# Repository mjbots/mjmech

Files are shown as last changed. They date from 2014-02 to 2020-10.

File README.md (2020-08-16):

mjmech
======

Source and design files for various walking robots, their controlling
interfaces, and utilities for developing and operating them.

* GitHub https://github.com/mjbots/mjmech
* Most files are free hardware and software: Apache 2.0 License
* buildkite 

Directory structure
-------------------

* **base/** - C++ source files common to many applications.
* **ffmpeg/** - C++ ffmpeg wrappers.
* **gl/** - C++ GL wrappers.
* **mech/** - C++ source files specific to walking robots.
* **simulator/** - C++ source files for a quadruped simulator.
* **utils/** - Utilities for development and data analysis.
* **video-ui/** - Client application for FPV and real-time control.
* **configs/** - Configuration files for different robots and applications.
* **hw/** - Hardware design files along with firmware.
* **docs/** - Documentation.

First Time Setup
----------------

The following should work on Ubuntu 18.04

```
./install-packages
```

Building for host
-----------------

```
tools/bazel test //...
```

Running simulation
------------------

```
./bazel-bin/simulator/simulator -c configs/quadruped.ini
```

Then point your web browser to `http://localhost:4778`

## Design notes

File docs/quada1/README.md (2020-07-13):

# Getting started with the quad A1 #

## Safety ##

The mjbots quad A1 is a high performance robot capable of very fast
and powerful motions.  It is not recommended for use in the vicinity
of untrained personnel and especially not children or others who do
not appreciate what it is capable of.

Minimize physical handling of the robot while the power switch is on,
as malfunctions may cause legs to to move rapidly, creating pinch
hazards.

## Turn on ##

1. Ensure the switch is in the "off" position.  When off, the LED side of the switch is *not* depressed.

2. Insert a 4Ah ONE+ battery.  It may be necessary to apply a moderate tap with your fist in order to get both retaining clips to latch.

3. Flip the quad A1 over to be right side up and extend legs to be maximally stretched out, flat against the ground.  This is the "turn-on" position.
  * NOTE: The software is able to detect *some but not all* invalid
    turn-on positions.

4. Activate the power switch.  This means pressing the side with the LED down.

5. After ~30s, the robot's wifi access point will become available.  Connect to it.

6. Point your web browser to http://192.168.16.47:4778

## Joystick ##

The web control application supports a connected gamepad, which is the
simplest means of controlling the robot.  The "Y/4" button on the
gamepad enables mode select, while the d-pad up and down allow you to
cycle between modes.  Once you pick a mode that is not "Stop", the
quad A1 will stand up.

While moving, the left analog stick controls translation, while the
left and right motion of the right analog stick controls yaw.

When stopped, the left trigger can be pulled to enable "emote mode".
In that mode, the analog sticks control the attitude of the body.

## Keyboard ##

It is also possible to operate the robot with a mouse and keyboard.
The mouse can be used to click and select a mode.  WASDQE keys can be
used to pilot the quad A1 as per the on-screen display.

# Maintenance #

## Belt tension ##

The leg belts need to be kept appropriately tensioned to minimize the
possibility of belt skipping, while not overly stressing the 3d
printed upper leg structure.  The M3 adjustment bolt in each leg can
be used to adjust that tension.  As the belts stretch with age, it
will likely be necessary to use a longer bolt than the M3x12 initially
installed.  M3x14 is the longest suitable bolt.

When tensioned properly,

## Rezeroing leg ##

If the leg is disassembled or re-assembled, or the belt skips, then that leg will need to be re-zeroed.  This can be accomplished as follows:

1. Lay the quad A1 upside down on a flat surface.
2. Install the leg zeroing fixtures on the leg in question.  The lower
   leg qdd100 rests on the curved part of the large fixture, and the
   upper part restrains the upper leg.
3. The smaller fixture registers the upper and lower leg together.
   Slide it down as far as possible, then attempt to get the lower leg
   as centered as possible in any remaining play.
4. Connect to the robot and stop the existing software:

```
ssh -i mjmech/utils/ssh/mjbots.ssh pi@192.168.16.47
sudo screen -r
<CTRL-c>
```

5. Determine the leg number of the leg to be rezeroed.  When looking
   from the top, the legs are numbered as follows (note the robot is
   upside down now, so this will be mirrored):

```
   1      2

     FRONT

     BACK

   3      4
```

6. Determine which servos are associated with that leg:

```
Leg 1: 1-3
Leg 2: 4-6
Leg 3: 7-9
Leg 4: 10-12
```

7. Rezero the leg, using the servo numbers from above.

```
./moteus_tool -t1-3 --zero-offset
```

8. If more legs need to be rezeroed, the fixture can be moved between
   legs and the step 7 command run more as necessary.

9. Shutdown the computer, wait 15s, then turn off the power switch.

```
shutdown -h now
```

10. At this point the quad A1 can be set in the "turn-on" position and
    started up as normal.

## Change ssh key ##

The quad A1 is initially provisioned with an ssh key that is common to
all machines.  This is not normally a problem, as the SSID is unique
and the password is secret.  If you wish to expose the quad A1 to a
wider network, first contact info@mjbots.com to discuss your risk
profile.  Second, you may wish to change the default ssh access key.

First, use `ssh-copy-id` to install a new key on the quad A1:

```
ssh-copy-id -o "-i utils/ssh/default.ssh" pi@192.168.16.47
```

Then, ssh in, and remove the old key.

```
ssh pi@192.168.16.47
vi .ssh/authorized_keys  # remove the info@mjbots.com line
```

## Upgrading software ##

1. Compile:

```
tools/bazel build --config pi -c opt //mech:quad_deploy.tar
```

2. Copy it to the robot:

```
rsync -Pv -e "ssh -i utils/ssh/default.ssh"  \
  bazel-out/armeabihf-opt/bin/mech/quad_deploy.tar pi@192.168.16.47:
```

3. Perform the upgrade and restart the software.

NOTE: If any configurations have been modified, you will want to
manually capture those now, as this process will reset all
configuration to factory default.

```
ssh -i utils/ssh/default.ssh pi@192.168.16.47
sudo screen -r
<CTRL-c>
cd /home/pi
sudo -u pi tar xvf quad_deploy.tar
sync
cd mech
./start-robot.sh
<CTRL-a d>
```

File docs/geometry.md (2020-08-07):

# mjmech geometry #

## Unit naming conventions ##

Quantities expressed in a certain unit should have that unit included
as a suffix that variable name.

## Frame naming conventions ##

Quantities which are expressed relative to some frame or frames have those frames suffixed on the variable name using the simbody conventions :https://simtk.org/docman/view.php/47/231/SimbodyTheoryManual.pdf

As there, common frames may be abbreviated with a single uppercase
letter.

## Frame conventions ##

Coordinate systems are right handed, if there is a human associated
direction, they should be interpreted as:

* x is positive forward
* y is positive right
* z is positive down

## Common frames ##

Joint Frame (J): Each joint has a frame located at the center of
rotation of the shoulder, with +x facing outward, +y facing right, +z
facing down.

Leg Frame (G): The leg frame is located at the center of the shoulder
joint, with +x facing forward, +y facing right, and +z facing down.

Body Frame (B): This frame is oriented at the center of the quadruped
body and fixed to the chassis.

CoM Frame (M): This frame is fixed to the chassis at the center of
mass as measured with the legs in idle position.  It is oriented to be
level with the ground, so +Z is always down w.r.t. gravity.  The frame
has a yaw such that +X is pointed to same heading as Body +X.

Attitude Frame (A): This frame is fixed to the chassis center of mass.
+Z is down w.r.t. gravity.  The rotation of +X/+Y is arbitrary at
power up, and follows the rotation of the B/L transform.

Robot Frame (R): This frame is offset from the Body Frame (B) and
referenced in the same manner, but may be offset or rotated to apply
cosmetic kinematic changes.

Terrain Frame (T): This frame is located at the center of mass,
projected along the body Z direction at the ground location.  It is
oriented parallel to the local ground terrain and rotated to be
consistent with the M frame.

Local Frame (L): This frame is oriented such that down is parallel to
gravity.  Other degrees of freedom are initialized with the quadrupeds
body center at turn on, and have no absolute correlation with the
outside world.

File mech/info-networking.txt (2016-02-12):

Networking setup for mjmech

================
High level goals
================

 (1) A reliable video and control channel which works even when 2.4GHz band is
     very busy.

 (2) A way to upload/debug new code. Does not have to be as reliable.

===================
Implementable goals
===================

 - Use dual-band 802.11n cards. 'n' should give us stream diversity, while 5GHz
   band will be likely less congested.

 - Do not use WiFi association mechanisms, to make sure that short periods of
   total interference stay short.

 - Customize queue length and retransmission, to make sure that at least some
   video appears, and that the latency is not too high.

 - Be able to change the system properties reasonably fast (in under a
   minute, not during the match).

==============
Current Design
==============

We are using ad-hoc mode, but specifying all the parameters ourselves.
This should be enough to ensure that we can start communicating without having
to wait for other station, and that we will not re-negotiate mid links.

We are logging all the packets and measuring the latencies.

To set up, use the script 'setup_wifi_link.py'. All wifi details are there.

IP addressing:
 - Devices have IP in the 10.89.0.0/16 network
  - Well-known devices have short addresses:
     mjmech-odroid has 10.89.0.10
 - Multicast network is 239.89.108.0/24
   239.89.108.10:2720 is multicast announcements from odroid
   239.89.108.11:2721 is control commands

=================
Wifi card comments
=================

We want a wifi card that supports 5GHz and 802.11n, at least. These have
problems.

Driver: rt2800usb
~~~~~~~~~~~~~~~~~
uses in-tree driver.
works great, but only tested in adhoc mode.

Devices:
* AWUS052NH, "ID 148f:3572 Ralink Technology, Corp. RT3572 Wireless Adapter"
 - Large black/orange box with 2x external antennas, Mini USB B Female connector
 - Front: orange, blue LED, "ALPHA NETWORKS", curved vent slots
 - Back: black, slot for clip, "Model: AWUS052NH", S/N, MAC, etc..
 - Size: 84.8x62x2.53mm + 24x10x8mm USB cable + 2x R10x160 antennas

* DWA-160, "ID 2001:3c1a D-Link Corp. DWA-160 802.11abgn Xtreme N Dual Band Adapter(rev.B2) [Ralink RT5572]"
 - Large white dongle with black border, large strap attachment point on top
 - Front: "D-LINK", orange WPS button, orange LED
 - Back: "D-LINK DWA-160", "P/N CWA160CA.....B2 Model: DWA-160B2",
         "H/W Ver: B2", "F/W Ver: 2.40", S/N, MAC
 - Size: 68.4x28.2x12mm + 12x12x4.5mm USB A plug

Known problems:
* problems connecting to regular wifi (WPA2 client) -- link disappears
  in 10-60 seconds
 - suspect this is due to old kernel (3.8.13)
 - do not really care

Driver: rtl8812au
~~~~~~~~~~~~~~~~~
Out-of-tree driver from: https://github.com/gnab/rtl8812au.git

Devices:
* Edimax AC600, "ID 7392:a812 Edimax Technology Co., Ltd"
 - Black dongle with with strap attachment point on top
 - Front: "EDIMAX AC"
 - Back: "WPS" button, "EW-7811UTC", "FCC ID..", etc..
 - Metal part of USB connector: I/C, SN, MAC
 - Size: 25.6x15.6x7.5mm + 12.2x12x4.5mm USB A plug

Known problems:
* problems connecting to regular wifi (WPA2 client)
 - do not care
* does not use nl80211 ('iw' command)
 - script special-cases, uses iwconfig
* multicast does not work (no packets go out)
 - fixed by patching the source: set 'psta->state |= _FW_LINKED'
   in 'rtw_init_bcmc_stainfo'
* cannot specify multicast rate (always 6Mbit/sec)
 - no fix known
* cannot force ad-hoc connection -- no way to set bssid
 - no fix known

Driver: mt7610u
~~~~~~~~~~~~~~~
Out-of-tree driver from: https://github.com/coolshou/mt7610u

Also works for chipsets:
 RT2870 RT2770 RT307X RT2070
 RT357X RT3370
 RT8070 RT5X7X
 MT7610 MT7601 MT7612U

Devices:
* AC600 WiFi Dual Band USB Adapter UW-600M01 "ID 0e8d:7610 MediaTek Inc."
 - Black dongle with the small pinhole in the center of one side
 - Only words on device itself is "wifi AC"
 - Box says: STRONGR-R AC600 / UW-600M01
 - Size: 15.1x14.9x8.1mm + 11.7x12x4.6mm USB plug

Potential other devices
~~~~~~~~~~~~~~~~~~~~~~~
This list is to filter out the devices which are not interesting for some reason
Hist: amazon search for "dual band wifi usb"

- Satechi Wireless Mini Dual Band Wi-Fi USB Mini Adapter ST-UMWAC
  rtl8812au according to amazon comments

- BlueFire Mini 150M USB WiFi Adapter B012G7H1YC
  not actually dual-band (2.4GHZ only)

- Glam Hobby 600Mbps AC600 Dual Band USB WiFi Dongle B011T5IF06
  driver link points to rtl8811au

- TRENDnet TEW-804UB Dual Band USB WiFi
  driver mentions RTL8811au, USB 20f4:804b

- Linksys Wireless Mini USB Adapter AC 580 Dual Band (AE6000)
  driver contains "RT2870" strings
  actual device is 13b1:003e, which seems to require mt7610u

- Sabrent AC600 Dual Band Wi-Fi USB Mini Adapter NT-WSAC
  driver file name is MT7601

- 'Intel Corporation Wireless 7260' (iwlwifi, integrated into thinkpad T430)
  does not support IBSS on 5GHZ band. Possible reason:
  "The firmware of (some?) Intel cards seems to prohibit the use of Band 2 in
  AP mode, and there is no workaround in driver or kernel code that I know
  of. "
  http://askubuntu.com/questions/457702/ubuntu-14-04-hostapd-802-11a-iwlwifi-no-ap

- "Motoraux 600Mbps Dual Band wireless" B0199FBBRM
 - driver unknown, TODO

- Woopower Wi-Fi Dual Band USB Adapter 5dBi Ext Antenna "AC600 MINI" B015SAFBRI
 - single external antenna
 - review has link to driver, which contains mt7610u code

- Bolse 300Mbps Wifi Wireless-N USB Micro Mini Adapter BO-N1557
 - has external antenna version (BO-N1559)
 - review says "Realtek RTL8192CU"

- Windrew 802.11AC 600mbps Dual Band 2.4G/5G UNT-W01
 - review says RT2870, other says to use driver for "EW-7711MAC"
 - this indicates mt7610u

- LB1 High Performance 600Mbps Dual Band USB UW-600M01-N0001
 - model number matches mt7610u part number

Testing wireless cards
~~~~~~~~~~~~~~~~~~~~~~
If you have a new wireless card, you can check it as following:

- Basic setup
(1) on main PC, set up wifi link and a monitor mode. run 'horst' on it.
 - In horst, enter 'ESSID' screen ('e' key), you should see the
   telemetry network.
 - bring wifi interface down on the main PC. the TSF value on horst will freeze.
 - bring wifi interface up on DUT.
 - Make sure TSF updates often and 'source' matches DUT's wireless MAC.
 - Make sure parameters (CH=channel, BSSID, BINT=beacon interval)
   match the configured ones.

(2) Start sending packets into 'empty space' (since PC has not joined yet)
 - In a new window:
tools/odroid/push-tree.sh odroid-mjmech \
  scons base/build-armv7l/udp_manual_test '&&' \
   base/build-armv7l/udp_manual_test -v \
      --link1.send_interval_s 0.005 --link1.source 239.89.108.11

 - The windows will print statistics every 10 seconds. Make sure packets are
   being sent. We do not expect to recevie anything at this time. Make sure it
   can maintain the send rate (there will be warnings if it cannot)
  INFO[link1]: stats: tx_count=2000 tx_size=2000000

 - In horst, switch to 'Stats' ('a' key)
  - You may want to 'R'eset the stats
  - Make sure prevalent rate is as configured in python (24M)
  - Make sure 'Retries' is very low and not growing.
  - Make sure 'Total bits/sec' is correct: 1.5M = 1000 bytes * 200 Hz
  - Make sure 'Total usage' is reasonable (for configuration descirbed above,
    it is 9-10%)

(3) on main PC, bring the wireless interface back up.
 - Make sure you can ping 10.89.0.10
 - On horst ESSID screen, make sure channel/BSSID did not change.

(4) Start sending
 - Window 1:
scons -j4 base/build-x86_64/udp_manual_test && \
   base/build-x86_64/udp_manual_test -v \
       --link1.send_interval_s 0.005 --link1.dest 239.89.108.11

 - Both windows will print statistics every 10 seconds. Make sure the packet
   loss is not excessively high:
  INFO[link1]: stats: rx[1]=1980 rx_count=1980 rx_size=1980000 tx_count=2000 tx_size=2000000

 - In horst, switch to 'Stats'.
  - Make sure rate and retries are still correct.
  - The 'Total bit/sec' will double.
  - The 'Total usage' willb bigger -- for configuration descirbed above, it is 24-25%

(5) Bring down the wireless interface on the main PC again.
 - Make sure the packets are still being sent as in item (2)

==============
Other options:
==============

Security
~~~~~~~~

We have to think about security -- in the large event, there may be all sorts
of people.

For reliability, we cannot use stateful security like WPA/WPA2. We may use WEP
eventually, but it will be disabled initially to simplify troubleshooting.

Attack: taking over robot
Status: not relevant -- we already use SSH to upload; assuming that our
application is not stupidly insecure, it will not provide any access to the
robot' OS.

Attack: taking over controlling laptop
Status: uses either our app or existing servers; our app should be fine, as long
at it is not stupidly unsecure; as for other apps, it is not worse than using
laptop in the coffee shop.

Attack: Denial of service.
Status: very likely possible, esp. if we crash on invalid packets. But wifi is
easily jammable anyway anyway. TODO theamk finish

Attack: information disclosure
Status: whatever. We have no confidential info over the channel (unless a
competitor incorporates it in their UI :) )

Robot link setup
~~~~~~~~~~~~~~~~

Our only option is usb<->wifi cards -- the robot has no other fast exposed
buses, and integrated wifi is not present / not dual-band.

Base station setup
~~~~~~~~~~~~~~~~~~

We need to be able to fully control base stations (obviously venue's AP will
not work, or may not be present at all). The options are:

- Dedicate a router for base station, hook it to laptop via ethernet.
 - PRO: may have very little latency if we write on-router daemon and card is
        connected via PCI.
 - PRO: nothing interferes with wifi setup
 - PRO: may be placed very close to the stage
 - CON: need to setup packet forwarding or write on-router daemon
 - CON: the dual-band N models may be large, require external power

- Use external USB card
 - PRO: small size, no external power supply needed.
 - PRO: May use the same type of the card the mech uses.
 - CON: USB adds some latency.
 - CON: NetworkManager will interfere.
  - Disable it completely (annoying as built-in wifi may be used during
    development / debugging).
  - May use network namespaces
   - This requires that anything that wants to talk to it has a root access.
   - Or we need to setup a 'virtual router' that needs the same
     packet-forwaring setup or router daemon that physical router requires.
  - May just add card's MAC to networkmanager ignore file
   - This is tricky to get right. Should probably script this.

- Use laptop's integrated network card
 - PRO: lower latency than USB-based cards
 - CON: intervet will not work if integrated card was used for it.
 - PRO: can just disable networkmanager's wifi entirely.
 - CON: not sure how good integrated antenna is.
 - CON: laptop's card may not be good enough, and we won't be able to use it.

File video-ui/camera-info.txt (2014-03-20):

Driver Info (not using libv4l2):
	Driver name   : uvcvideo
	Card type     : HD Pro Webcam C920
	Bus info      : usb-s5p-ehci-3.2
	Driver version: 3.8.13
	Capabilities  : 0x84000001
		Video Capture
		Streaming
		Device Capabilities
	Device Caps   : 0x04000001
		Video Capture
		Streaming
Priority: 2
Video input : 0 (Camera 1: ok)
Format Video Capture:
	Width/Height  : 1920/1080
	Pixel Format  : 'H264'
	Field         : None
	Bytes per Line: 3840
	Size Image    : 4147200
	Colorspace    : SRGB
Crop Capability Video Capture:
	Bounds      : Left 0, Top 0, Width 1920, Height 1080
	Default     : Left 0, Top 0, Width 1920, Height 1080
	Pixel Aspect: 1/1
Streaming Parameters Video Capture:
	Capabilities     : timeperframe
	Frames per second: 30.000 (30/1)
	Read buffers     : 0
                     brightness (int)    : min=0 max=255 step=1 default=128 value=128
                       contrast (int)    : min=0 max=255 step=1 default=128 value=128
                     saturation (int)    : min=0 max=255 step=1 default=128 value=128
 white_balance_temperature_auto (bool)   : default=1 value=1
                           gain (int)    : min=0 max=255 step=1 default=0 value=201
           power_line_frequency (menu)   : min=0 max=2 default=2 value=2
      white_balance_temperature (int)    : min=2000 max=6500 step=1 default=4000 value=2354 flags=inactive
                      sharpness (int)    : min=0 max=255 step=1 default=128 value=128
         backlight_compensation (int)    : min=0 max=1 step=1 default=0 value=0
                  exposure_auto (menu)   : min=0 max=3 default=3 value=3
              exposure_absolute (int)    : min=3 max=2047 step=1 default=250 value=416 flags=inactive
         exposure_auto_priority (bool)   : default=0 value=1
                   pan_absolute (int)    : min=-36000 max=36000 step=3600 default=0 value=0
                  tilt_absolute (int)    : min=-36000 max=36000 step=3600 default=0 value=0
                 focus_absolute (int)    : min=0 max=250 step=5 default=0 value=0 flags=inactive
                     focus_auto (bool)   : default=1 value=1
                  zoom_absolute (int)    : min=100 max=500 step=1 default=100 value=100

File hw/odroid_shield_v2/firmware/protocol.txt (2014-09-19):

The device shares the serial bus with herculex, so the protocol
is fulley herculex compatible.

AVR listens at 115200 (divisor 16 in high-speed mode, 2.1% error)

It does not handle broadcasts because this it too much pain.

The device sits on address 99, and supports the following commands:
  CMD_STAT
  CMD_REBOOT -- does not reboot, just clears outputs and error flags.
  CMD_RAMWRITE/CMD_RAMREAD -- limited addresses
    - read address and status

    - read/write LEDS (53):
      GREEN is green LED pin (nothing is there yet)
      RED   is laser output
      BLUE  is blue LED on the board
      unlike real servo, if no LED commands are given for few
      seconds, all LEDs are turned off

    - read/write FIRE TIME (80, reserved)
      This is 1-byte register which can be read and written.
      As long as it is non-zero:
       - FIRE PWM may be non-zero
       - Value decreases by 1 every 10 mS

    - read/write FIRE PWM (81, reserved)
      This is 1-byte register which sets PWM value for fire motor.
      (0 = off, 255 = continious high)
      It is continously forced to zero unless FIRE CONTROL is set.

    - read/write AGITATOR PWM (82, reserved)
      This is 1-byte register which sets PWM value for agitator motor.
      (0 = off, 255 = continious high)
      It is bound to LED activity -- if LEDs are not updated for a while,
      then this value is forced to zero. Thus, you will want to write
      to LED register at the same time as to this register.

    - LEDS alias: (83, reserved) -- exactly the same as 53
      allows one-command access to agitator pwm

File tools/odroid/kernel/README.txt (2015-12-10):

Compiling custom kernel

-----------------------------
Motivation:

The linux kernel in the odroid distribution we are using is based on 3.8.13.30
kernel modified by hardkernel. This has two problems:
(1) there is no 'build' directory, so it is impossible to build out-of-tree
drivers.
(2) some wireless drivers are too old (such as rt2800usb)

There are some instructions on how to partially rebuild a kernel to fix (1),
but if we are going to make our own kernel, we migh t as well go to mainline.

Stock kernel info:
uname: 3.8.13.30 #1 SMP PREEMPT Fri Sep 4 23:45:57 BRT 2015 armv7l armv7l armv7l GNU/Linux
vermagic (from modinfo): 3.8.13.30 SMP preempt mod_unload ARMv7 p2v8
ABI ('file' on module): 32-bit LSB relocatable, ARM, EABI5 version 1 (SYSV)
source: git clone https://github.com/hardkernel/linux.git -b odroid-3.8.y

Inspiration:
http://rglinuxtech.com/?p=1622 (and other posts on this blog)

Instructions:
https://mescanef.net/blog/2014/12/custom-kernel-compilation-for-odroid-u2-u3-on-host-running-fedora-linux/

-----------------------------
Preparation:
possibly "mainline kernels need an updated u-boot to successfully boot."
http://rtisat.blogspot.com/2015/04/a-little-progress.html

I updated the u-boot via odroid-utility.sh

luckily, initrd does not seem to contain any kernel modules.
check with:
dd bs=64 skip=1 if=/media/boot/uInitrd  | zcat | cpio --list | less

New kernel needs new u-boot, which can be updated per blog post above.
Run the following on the odroid:
    aptitiude install device-tree-compiler
    wget http://odroid.in/guides/ubuntu-lfs/boot.tar.gz
    tar xzf boot.tar.gz
    git clone https://github.com/tobiasjakobi/u-boot
    cd u-boot
    make odroid_config
    make
    cp u-boot-dtb.bin ../boot/u-boot.bin

    echo 0 | sudo tee /sys/block/mmcblk0boot0/force_ro
    sudo dd iflag=dsync oflag=dsync if=./u-boot-dtb.bin of=/dev/mmcblk0boot0 seek=62

    cd ../boot
    bash ./sd_fusing.sh /dev/mmcblk0

                        signed_bl1_position=0
                        bl2_position=30
                        uboot_position=62
                        tzsw_position=2110

(the old kernels still work after this procedure)
u-boot version after:
  Exynos4412 # version
  U-Boot 2010.12-svn (May 12 2014 - 15:05:46) for Exynox4412

uboot update: see /usr/local/bin/kernel_update.sh

-----------------------------
Process:
We do a cross-compile on a x86_64 machine.

(1) download the kernel, prepare the build dir
 sudo apt-get install gcc-4.7-arm-linux-gnueabi gcc-arm-linux-gnueabi
 # the kernels are extracted as root, and thus read-only. make the build dir.
 sudo install -d -o $UID /usr/src/kernel-odroid

(1a) get the stock kernel. note
 cd /tmp
 wget https://cdn.kernel.org/pub/linux/kernel/v4.x/linux-4.3.tar.xz
 sudo tar xJf linux-4.3.tar.xz -C /usr/src
  get the odroid kernel

(2) configure kernel:
note: always use 'kmake.sh' instead of make in kernel dir, or you many get
options related to x86 kernel. It also move .config file location inside
the tree, so 'git diff' becomes more helpful.

use previous configuration with new things set as modules:
 rm tools/odroid/kernel/config-linux-4.3
 KCONFIG_ALLCONFIG=$PWD/tools/odroid/kernel/config-hardkernel-3.8.13.30 tools/odroid/kernel/kmake.sh allmodconfig
OR use previous configuration with new things set as default:
 cp tools/odroid/kernel/config-hardkernel-3.8.13.30 tools/odroid/kernel/config-linux-4.3
 tools/odroid/kernel/kmake.sh olddefconfig

the enter/exit menunconfig to inspect it by hand and update the config:
 tools/odroid/kernel/kmake.sh menuconfig
 # pay attention to options with '(NEW)'
 # make sure to clear CONFIG_EXTRA_FIRMWARE if using mainline kernels
 # make sure to CONFIG_MODULE_COMPRESS is not set

(3) build and copy modules
 time tools/odroid/kernel/kmake.sh -j4 zImage modules
 tools/odroid/kernel/kmake.sh modules_install firmware_install zinstall

 # Check version
 tools/odroid/kernel/kmake.sh -s kernelrelease
 # optionally delete old modules
 rm /usr/src/kernel-odroid/linux-4.3-install/boot/*.old
 ssh odroid@odroid-mjmech rm -rf /lib/modules/4.3.0-mjmech1 /lib/firmware-linux-4.3
 # copy all files over (this will not activate them yet)
 rsync -av --rsync-path='sudo rsync' /usr/src/kernel-odroid/linux-4.3-install/ odroid@odroid-mjmech:/

 # copy to /boot partition
 odroid@odroid-mjmech# sudo cp /boot/exynos4412-odroidu3.dtb /media/boot/
 odroid@odroid-mjmech# sudo cp /boot/vmlinuz-4.3.0-mjmech1 /media/boot/zImage-4.3
 sudo mkimage -T script -d kernel-4.3.script kernel-4.3.scr

(4) activate the new kernel
 odroid@odroid-mjmech# sudo cp kernel-4.3.scr boot.scr
 odroid@odroid-mjmech# sudo reboot

--------
recovery procedure
- connect serial port, open at 115200
- press any key during countdown
- run the original boot script (old bootloader)
fatload mmc 0:1 40008000 boot-auto_edid.scr
run bootscript
# if the bootloader has been updated, the last step will fail; in this case, run:
bootz  0x40008000 0x42000000

- once booted, restore original script:
odroid@odroid-mjmech$ cd /media/boot
odroid@odroid-mjmech$ sudo cp boot-auto_edid.scr boot.scr
odroid@odroid-mjmech$ sudo /usr/local/bin/odroid-utility.sh
# select 'update bootloader'

- examine the current config (or just see the boot.scr file on original image)
Exynos4412 # printenv bootcmd
bootcmd=    cfgload; mmc rescan 0:1; mmc rescan 0:2;  if run loadbootscript_1;     then run bootscript;  else     if run loadbootscript_2;  |
Exynos4412 # cfgload
do_fat_cfgload : cmd = fatload mmc 0:1 0x41000000 boot.ini
reading boot.ini
** Unable to read file boot.ini **
Exynos4412 # printenv loadbootscript_1
loadbootscript_1=echo >>> Load Boot Script from mmc 0:1 <<<;fatload mmc 0:1 40008000 boot.scr
Exynos4412 # run loadbootscript_1
>>> Load Boot Script from mmc 0:1 <<<
reading boot.scr
Warning : Reads a file that is smaller than the cluster size.
380 bytes read in 34 ms (10.7 KiB/s)
Exynos4412 # printenv bootscript
bootscript=source 40008000
Exynos4412 # md 40008000 75
40008000: 56190527 379fda4f 3e2d7d52 3c010000    '..VO..7R}->...<
40008010: 00000000 00000000 39df7f05 00060205    ...........9....
40008020: 746f6f62 7263732e 726f6620 77205820    boot.scr for X w
40008030: 20687469 494d4448 74756120 72702d6f    ith HDMI auto-pr
40008040: 34010000 00000000 65746573 6920766e    ...4....setenv i
40008050: 7274696e 69685f64 22206867 66667830    nitrd_high "0xff

- run stored commands using different kernel name
setenv initrd_high "0xffffffff"
setenv fdt_high "0xffffffff"
setenv bootcmd "fatload mmc 0:1 0x40008000 zImage.0; fatload mmc 0:1 0x42000000 uInitrd; bootm 0x40008000 0x42000000"
setenv edid_load "drm_kms_helper.edid_firmware=edid/1024x768.bin"
setenv bootargs "console=tty1 console=ttySAC1,115200n8 ${edid_load} root=UUID=e139ce78-9841-40fe-8823-96a304a09859 rootwait ro  mem=2047M"
boot

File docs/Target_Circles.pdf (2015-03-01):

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

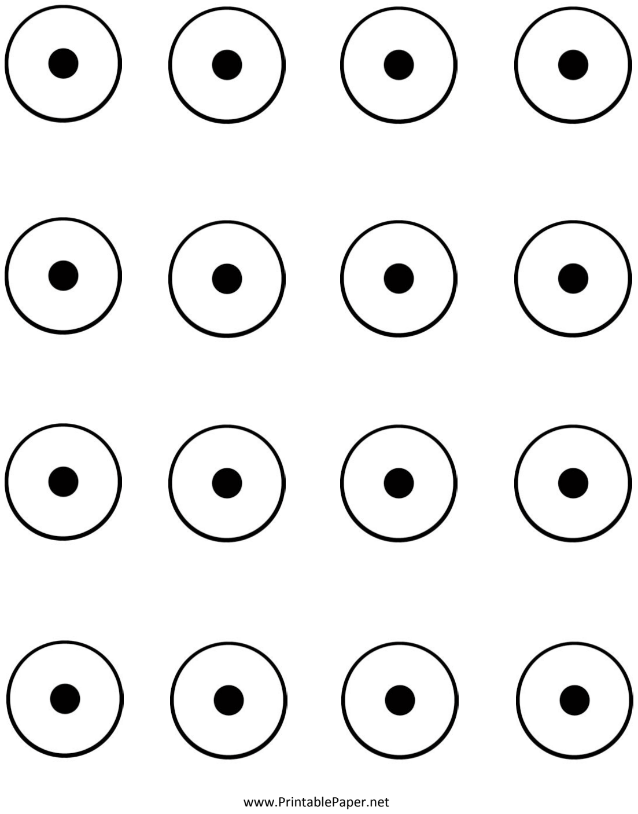
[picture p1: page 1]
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

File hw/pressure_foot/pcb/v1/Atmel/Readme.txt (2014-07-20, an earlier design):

						This CAD library is for CadSoft - EAGLE tool

How to import new library file (.lbr) into EAGLE:

1. Download and extract the file.
2. Copy the library file (.lbr) to EAGLE library folder; "C:\Program Files\EAGLE-X.XX.X\lbr" (X.XX.X is your EAGLE software version)
3. Start EAGLE software.
4. Under EAGLE Control Panel, go to the Library tree and browse for new copied library (.lbr) file.
5. Right click on the library and select "USE".
6. You have successfully imported new library and ready to use in your design.  

=============================================================================================================================================================

				For additional information, feedback and Technical support please contact reach from below:

Tech Support e-mail  ::	CAD_Tech@element14.com

----------------------------------------------------

Community website  

	http://www.element14.com/community/community/knode/cad_tools?view=overview

=============================================================================================================================================================

element14 Disclaimer :- 
 
This information has been provided to you free of charge for your use but remains the sole property of element14. While element14 has used reasonable efforts to ensure its accuracy, element14 does not guarantee that it is error-free, nor makes any warranty or guarantee as to the suitability of its schematics or footprints for any specific application. element14 reserves the right to make changes at any time without further notice. element14 expressly disclaims all implied warranties regarding this information, including but not limited to any implied warranties or merchantability or fitness for a particular purpose.
 
element14 will in no case be liable for your use, or the results of your use, of the CAD models or any accompanying written materials. It is your responsibility to verify the results of your use of this information in your own particular engineering and product environment and you assume the entire risk of doing so or failing to do so. 
 
Footprint designs were developed using standard layout guidelines for most common and practical applications. All schematic symbols, footprints and layer definitions should be validated by the customer’s own technical experts as application specific requirements may differ.

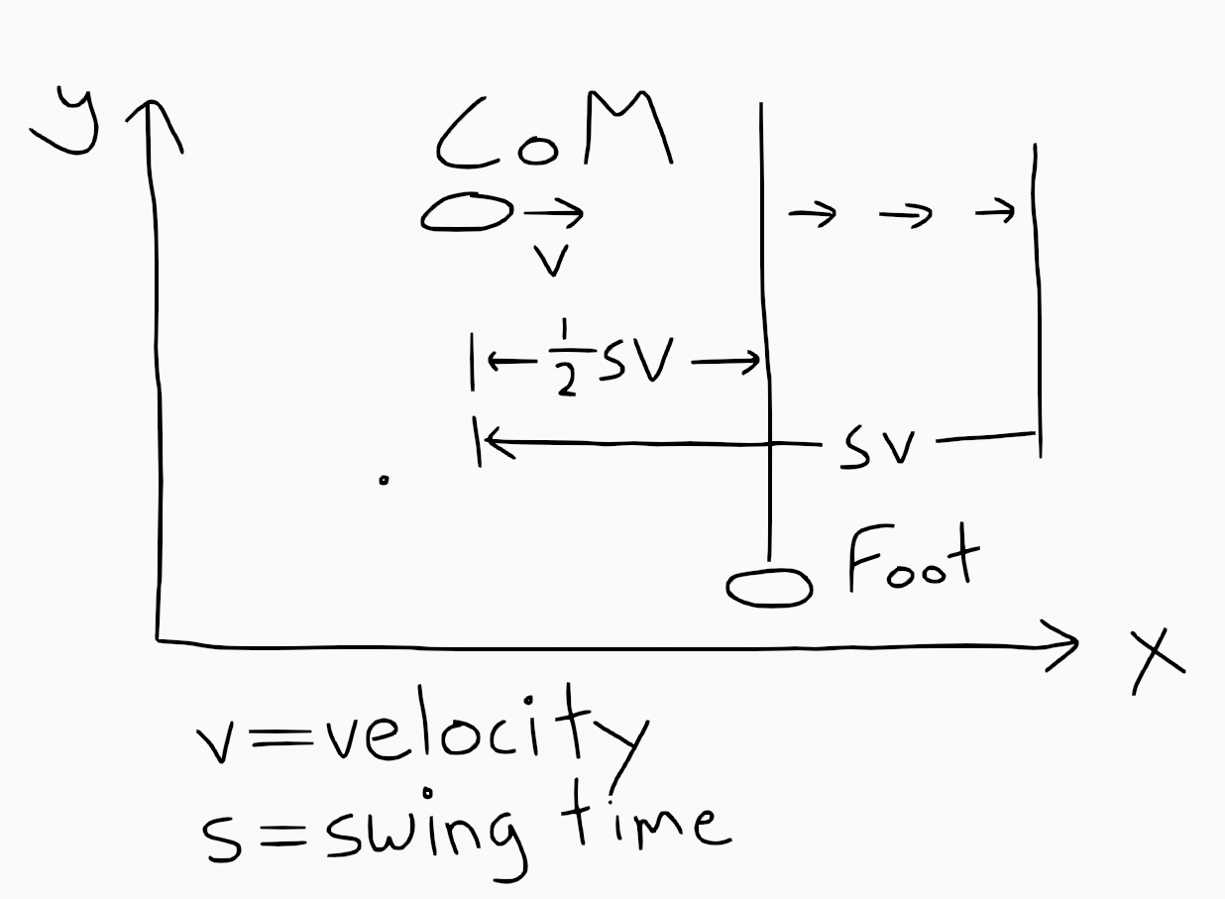
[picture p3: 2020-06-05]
docs/diagrams/1d_swing.png

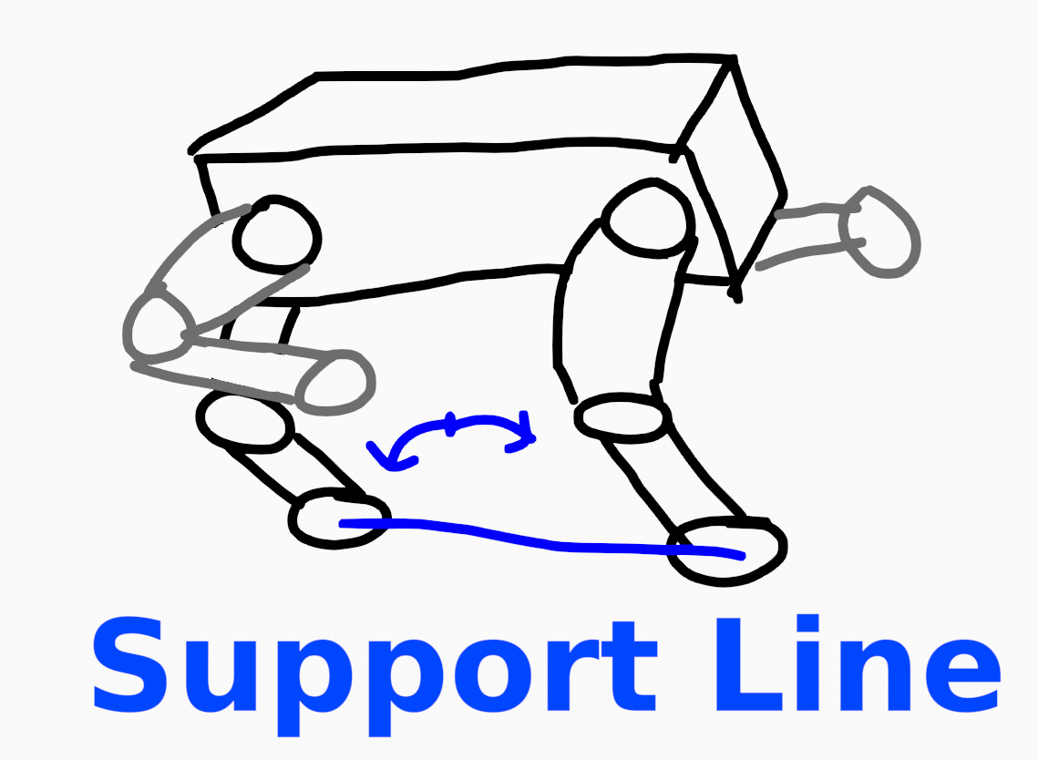
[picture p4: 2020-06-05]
docs/diagrams/support_line.png

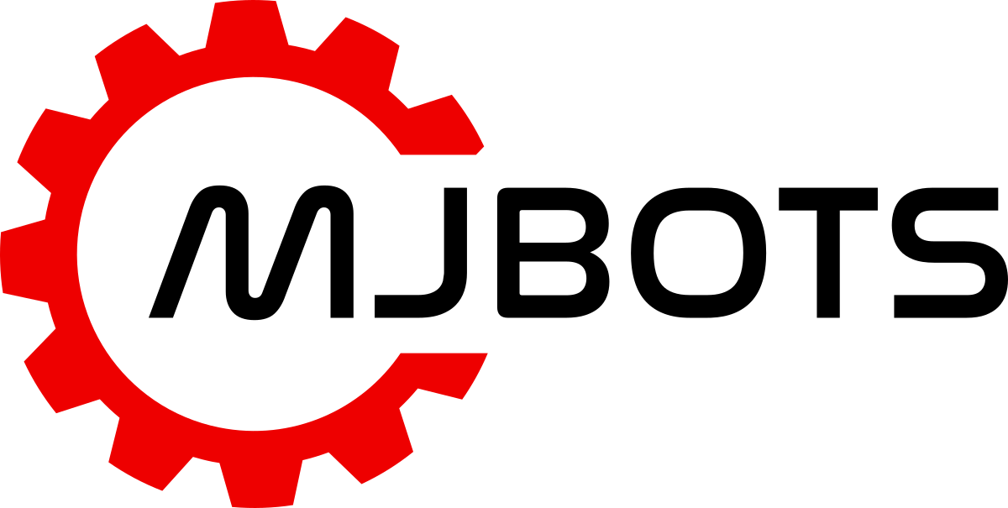
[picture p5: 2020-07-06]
mech/web_control_assets/mjbots.png

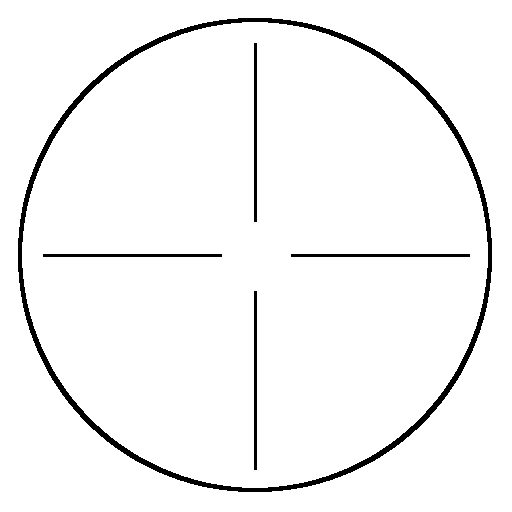
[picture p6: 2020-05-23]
mech/reticle.png

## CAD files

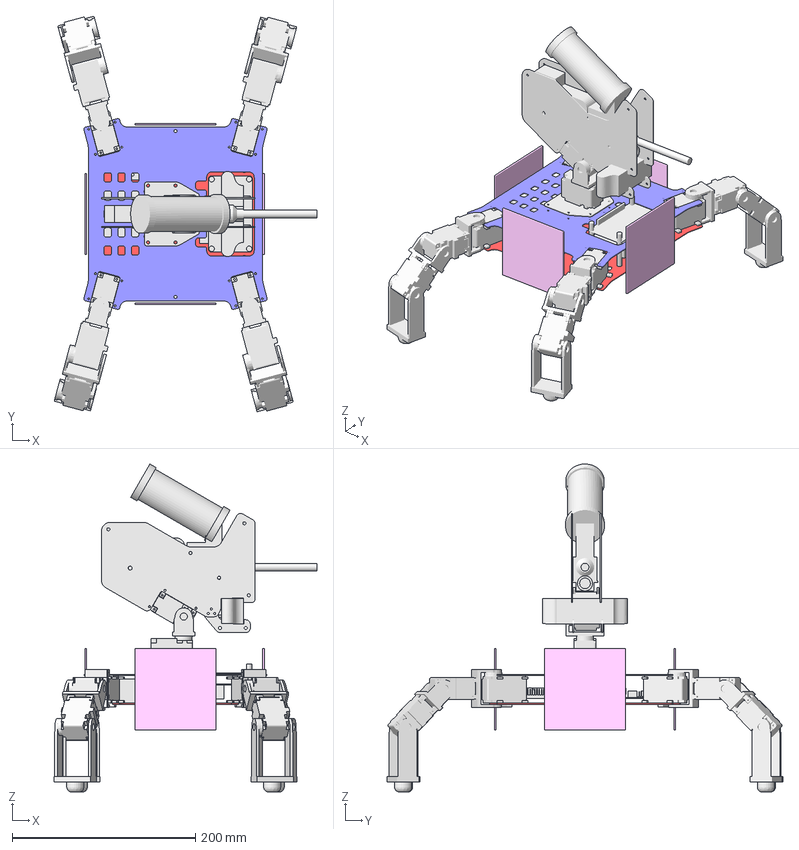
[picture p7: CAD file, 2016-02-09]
hw/chassis_lizard/freecad/chassis.fcstd
286.8 x 432.0 x 358.2 mm
pololu_driver
battery
power_dist
leg
scoring_transponder
leg2
leg3
leg4
sensor
sensor2
sensor3
sensor4
odroid
i_beam1
i_beam2
i_beam3
i_beam4
chassis_bottom_harness_holes
chassis_top_turret_holes
turret_plate_gimbal_holes
turret

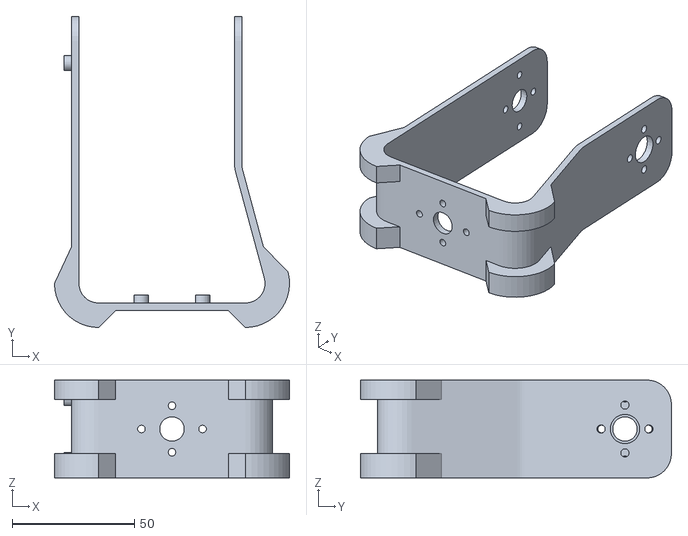
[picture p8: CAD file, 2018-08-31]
hw/chassis_mammal/freecad/gimbal_bracket.stl
96.0 x 127.0 x 40.0

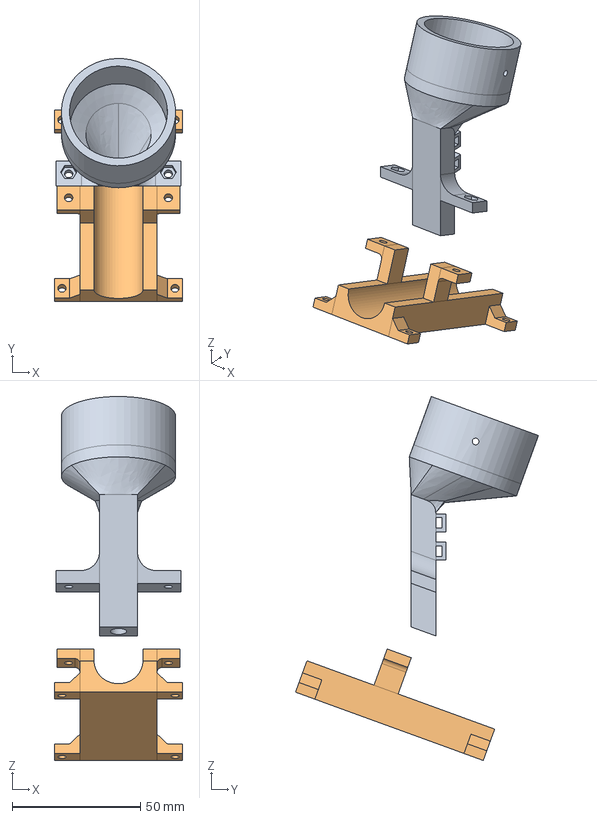
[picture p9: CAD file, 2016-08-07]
hw/panel_qual/freecad/gravity_feed.fcstd
50.0 x 94.6 x 141.7 mm

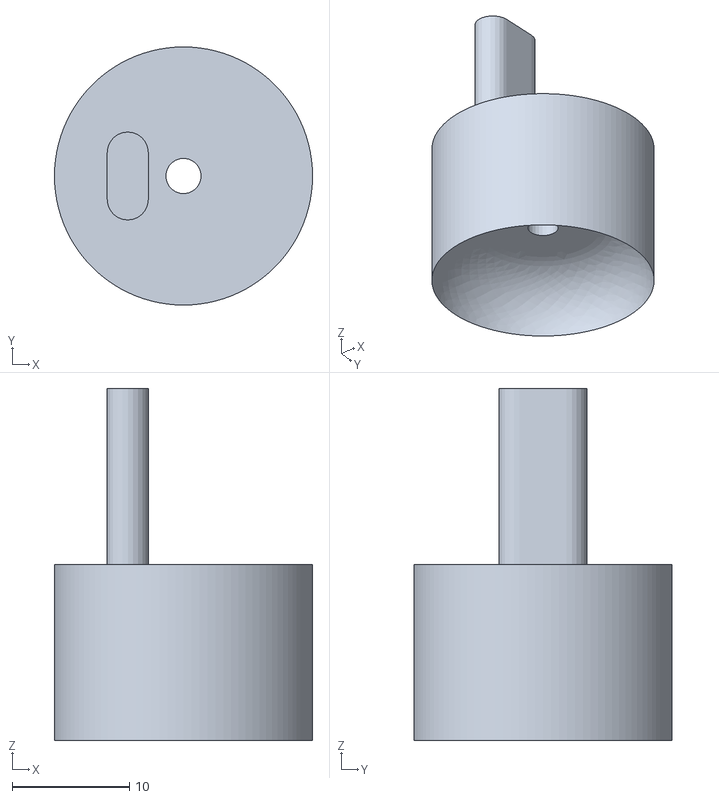
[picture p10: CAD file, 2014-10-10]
hw/pressure_foot/freecad/plunger.stl
22.0 x 22.0 x 30.0

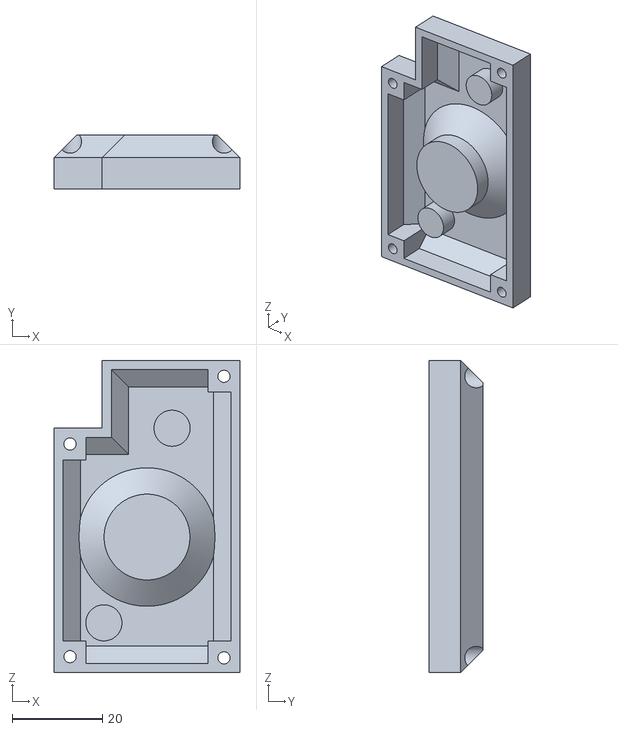
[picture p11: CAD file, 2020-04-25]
hw/turret/aeg_20200418/loader_cap.stl
41.1 x 12.0 x 69.1

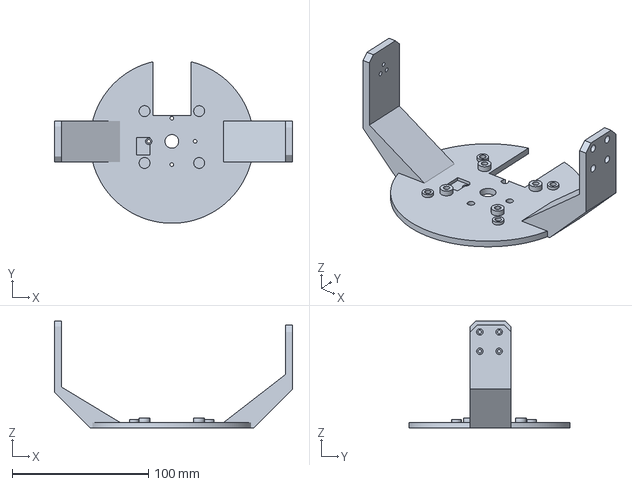
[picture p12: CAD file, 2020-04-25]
hw/turret/aeg_20200419/yaw_motor_plate.3mf
174.4 x 118.3 x 78.2 mm

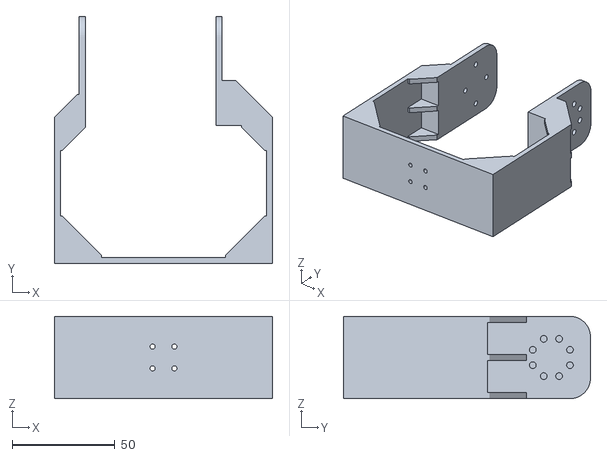
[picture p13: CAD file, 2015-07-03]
hw/turret/freecad/gimbal_bracket.stl
106.0 x 120.0 x 40.0

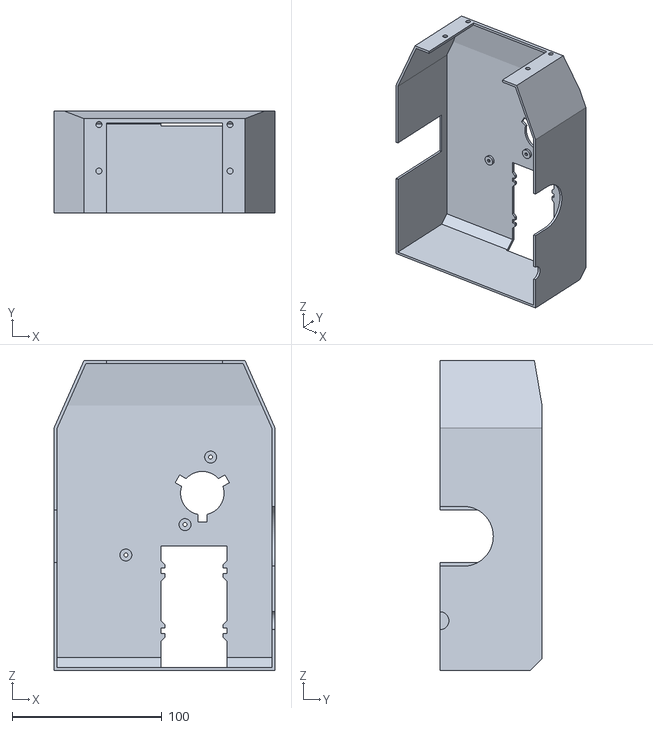
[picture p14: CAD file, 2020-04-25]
hw/turret/turret_20200420/shell_top.stl
147.6 x 68.2 x 207.1

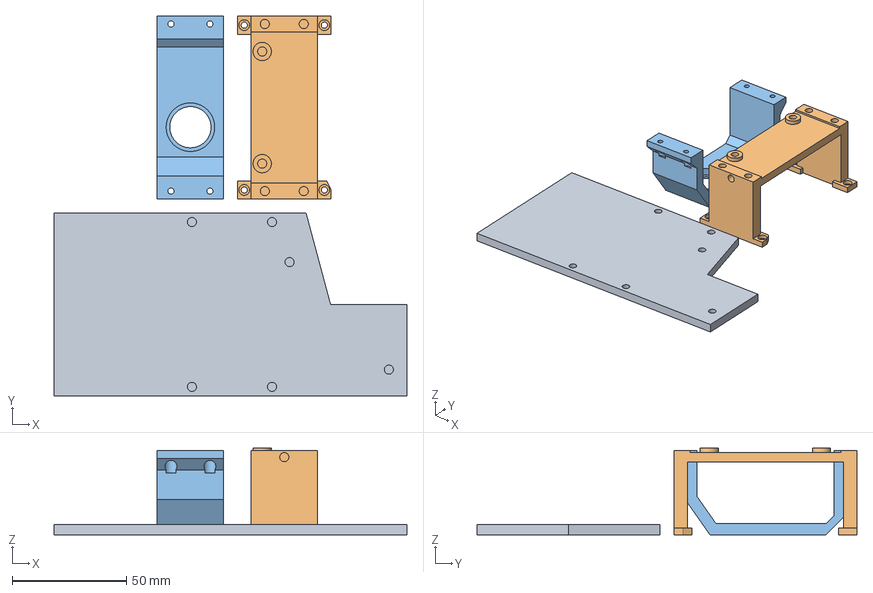
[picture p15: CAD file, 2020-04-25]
hw/turret/turret_20200421-2/mid_frame_right_frame_rpitch_plate.3mf
154.0 x 166.0 x 38.0 mm
mid_frame.stl
right_frame.stl
right_pitch_plate.stl

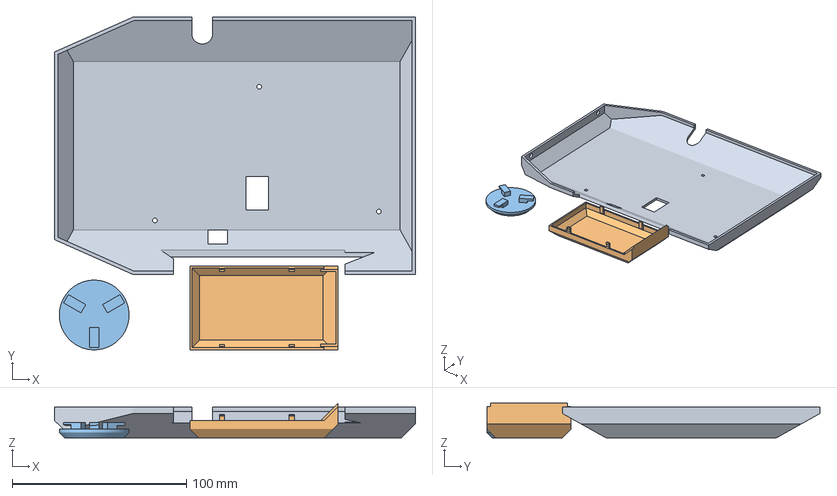
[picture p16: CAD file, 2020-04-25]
hw/turret/turret_20200421/shell_bottom_accessories.3mf
207.1 x 190.8 x 20.0 mm
shell_bottom.stl
shell_battery_cover.stl
shell_magazine_cover.stl

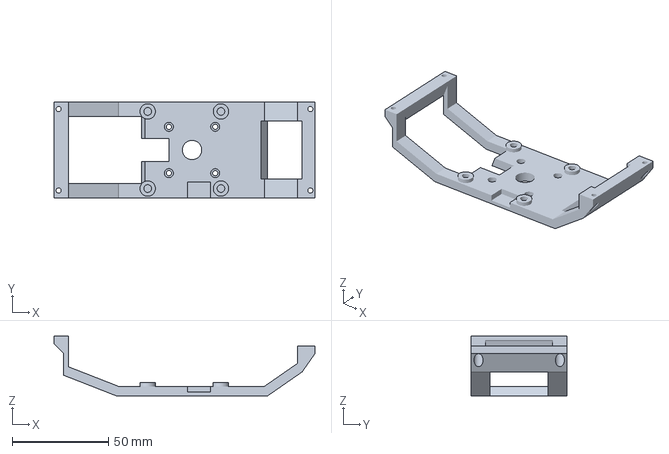
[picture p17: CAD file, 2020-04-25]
hw/turret/turret_20200422/pitch_motor_plate.3mf
135.5 x 50.0 x 31.1 mm

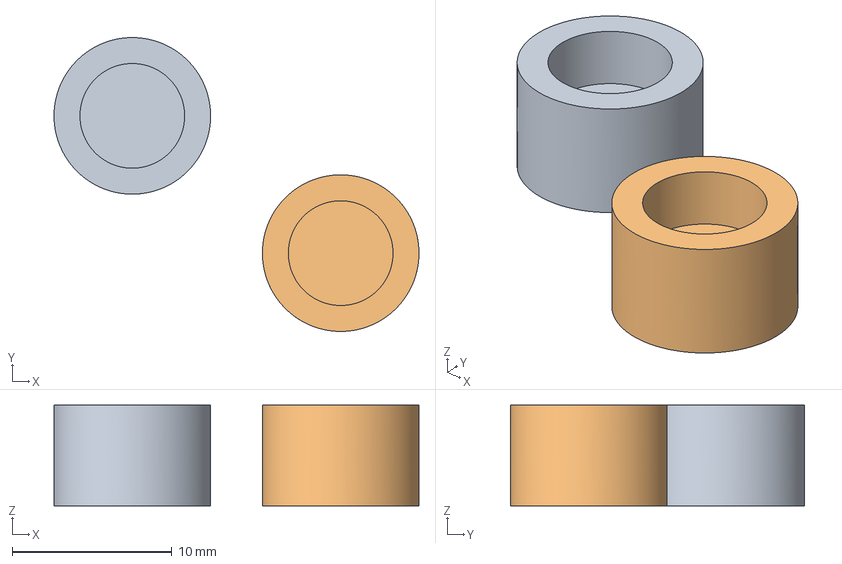
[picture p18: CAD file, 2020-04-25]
hw/turret/turret_20200423/magnet_holder.3mf
22.8 x 18.4 x 6.30 mm

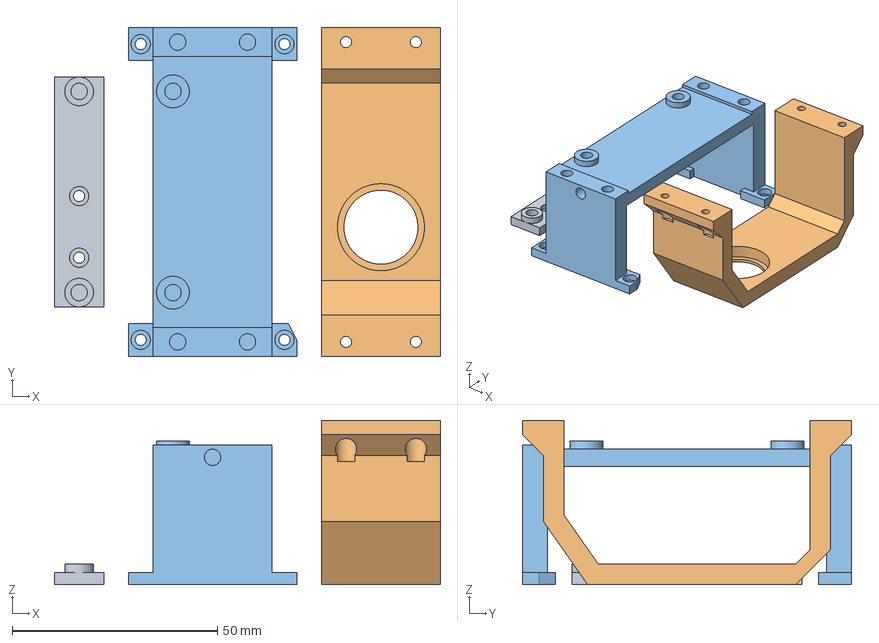
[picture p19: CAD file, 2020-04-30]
hw/turret/turret_20200430/right_brackets.3mf
94.0 x 80.0 x 40.0 mm
front_pi_bracket.stl
right_pitch_plate.stl
right_frame.stl

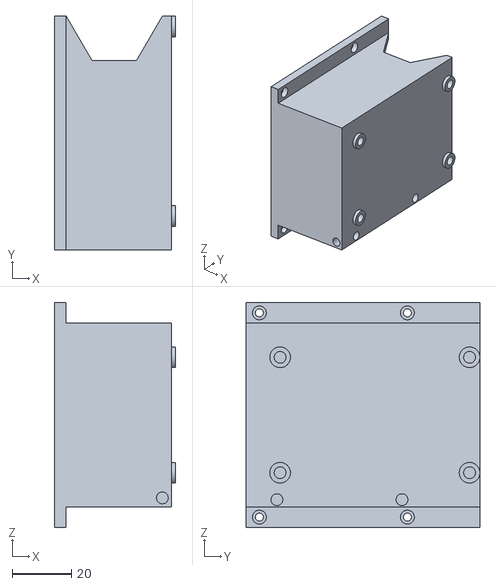
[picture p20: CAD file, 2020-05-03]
hw/turret/turret_20200501/battery_shelf.stl
41.0 x 79.0 x 76.0

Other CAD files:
hw/turret/turret_20200502/top.3mf
hw/turret/turret_20200516/battery_cover.3mf
hw/turret/turret_20200517/battery_cover_2.stl
hw/weapon/aeg_20200414-2/receiver.3mf
docs/diagrams/1d_swing.blend
docs/diagrams/support_line.blend
hw/chassis_lizard/freecad/battery.fcstd
hw/chassis_lizard/freecad/battery.step
hw/chassis_lizard/freecad/bracket_long_tip.blend
hw/chassis_lizard/freecad/bracket_long_tip.fcstd
hw/chassis_lizard/freecad/bracket_long_tip.iges
hw/chassis_lizard/freecad/bracket_short.fcstd
hw/chassis_lizard/freecad/bracket_short.iges
hw/chassis_lizard/freecad/bracket_short_0_join.fcstd
hw/chassis_lizard/freecad/bracket_short_0_join.iges
hw/chassis_lizard/freecad/bracket_short_90_join.fcstd
hw/chassis_lizard/freecad/bracket_short_90_join.iges
hw/chassis_lizard/freecad/bracket_u1.fcstd
hw/chassis_lizard/freecad/bracket_u1.iges
hw/chassis_lizard/freecad/bracket_u4.fcstd
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

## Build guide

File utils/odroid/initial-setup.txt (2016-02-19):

New Odroid setup procedure
Using Odroid U3+

(1) Start by plugging eMMC card into your computer. Get an small
"Ubuntu 14.04 Server" image from:
  http://forum.odroid.com/viewtopic.php?f=77&t=5123
  http://odroid.in/ubuntu_14.04lts/

mkdir -p /tmp/odroid-image && cd /tmp/odroid-image
wget http://odroid.in/ubuntu_14.04lts/ubuntu-14.04lts-server-odroid-u-20140604.img.xz
md5sum ubuntu-14.04lts-server-odroid-u-20140604.img.xz
# b7568e191eef679116e252ae5136ecee  ubuntu-14.04lts-server-odroid-u-20140604.img.x

  Then extract it to the eMMC card:
ls -l /dev/disk/by-path/*-usb-*:[0-9]
xzcat *lts-server*.xz | sudo dd bs=1M of=/dev/sdXX
# 3384803328 bytes (3.4 GB) copied, 268.485 s, 12.6 MB/s
sync

(2) Do the initial setup:
# Plug wired ethernet and power. Device should appear as 'odroid-server':
ssh -o UserKnownHostsFile=/dev/null -o StrictHostKeyChecking=no root@odroid-server
# password: odroid
odroid-utility.sh
# choose "4  Resize your root partition"
# choose "7  Change Hostname"
#  -> Examples below use "odroid-mjmech"
# choose "2  Update your Kernel/Firmware"
#  -> choose "1 Update Kernel"
#  -> choose "2 Install firmware files to /lib/firmware"
# exit all
useradd -Um odroid
chsh -s /bin/bash odroid
passwd odroid
visudo
# add the line:
  odroid  ALL=NOPASSWD: ALL
# logout, install ssh public key
ssh-copy-id -i ~/.ssh/id_dsa.pub odroid@odroid-mjmech
ssh odroid@odroid-mjmech sudo uptime

(3) Upload the code and configure the devices:
tools/odroid/push-tree.sh odroid-mjmech sudo tools/odroid/setup-system.sh
# if you this fails, ssh into device and run:
sudo apt-get update
sudo apt-get upgrade
sudo mjmech-clean/tools/odroid/setup-system.sh

(4) Setup wifi auth and reboot:
ssh odroid@odroid-mjmech -t sudo editor /etc/wpa_supplicant/wpa_supplicant.conf
ssh odroid@odroid-mjmech -t sudo reboot
# You may wish to unplug wired ethernet at this point.

(5) Do the initial build:
tools/odroid/push-tree.sh odroid-mjmech time scons
# real 41m45.404s / user 40m8.325s / sys 1m22.815s

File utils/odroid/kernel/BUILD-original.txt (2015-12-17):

Re-compiling original odroid kernel

STATUS: Successful -- system boots fine

-----------------------------
# Trying to follow instructions as close as possible:
#  https://mescanef.net/blog/2014/12/custom-kernel-compilation-for-odroid-u2-u3-on-host-running-fedora-linux/
# Differences:
#  (1) rpm ugliness since we are on deb system
#  (2) easier deploy -- new script, --rsync-path trick

cd /local2/odroid2

# get linux sources
git clone https://github.com/hardkernel/linux.git -b odroid-3.8.y

# get toolchain
mkdir rpm && cd rpm
TC1=https://copr-be.cloud.fedoraproject.org/results/lantw44/arm-linux-gnueabi-toolchain/fedora-20-x86_64
wget $TC1/arm-linux-gnueabi-binutils-2.25-2.fc21/arm-linux-gnueabi-binutils-2.25-2.fc20.x86_64.rpm
wget $TC1/arm-linux-gnueabi-gcc-5.1.0-2.fc21/arm-linux-gnueabi-gcc-5.1.0-2.fc20.x86_64.rpm
wget $TC1/arm-linux-gnueabi-glibc-2.21-2.fc21/arm-linux-gnueabi-glibc-2.21-2.fc20.x86_64.rpm
wget ftp://rpmfind.net/linux/fedora/linux/updates/21/x86_64/i/isl-0.14-3.fc21.x86_64.rpm
wget ftp://rpmfind.net/linux/fedora/linux/updates/21/x86_64/g/gmp-6.0.0-9.fc21.x86_64.rpm

rpm2cpio arm-linux-gnueabi-binutils-2.25-2.fc20.x86_64.rpm | cpio -dium
rpm2cpio arm-linux-gnueabi-gcc-5.1.0-2.fc20.x86_64.rpm | cpio -dium
rpm2cpio arm-linux-gnueabi-glibc-2.21-2.fc20.x86_64.rpm | cpio -dium
rpm2cpio isl-0.14-3.fc21.x86_64.rpm | cpio -dium
rpm2cpio gmp-6.0.0-9.fc21.x86_64.rpm | cpio -dium

cd ..

# configure
odroid_tc=${PWD}/rpm/usr/bin/arm-linux-gnueabi-
export LD_LIBRARY_PATH=${PWD}/rpm/usr/lib64
${odroid_tc}gcc -v
# gcc version 5.1.0 (GCC)
cd linux
CORES=4 LOADADDR=40008000 ARCH=arm CROSS_COMPILE=$odroid_gcc make odroidu_defconfig
CORES=4 LOADADDR=40008000 ARCH=arm CROSS_COMPILE=$odroid_gcc make menuconfig
# in 'General Setup', set 'Local Version' to '-at2'

# build and copy
CORES=4 LOADADDR=40008000 ARCH=arm CROSS_COMPILE=$odroid_gcc make -j4 uImage zImage modules
mkdir -p modules/media/boot
CORES=4 LOADADDR=40008000 ARCH=arm CROSS_COMPILE=$odroid_gcc make modules_install  INSTALL_MOD_PATH="modules/"
cp arch/arm/boot/zImage modules/media/boot/zImage-at2
#cp arch/arm/boot/uImage modules/media/boot/uImage-at2
rsync -av --no-owner --no-group --rsync-path='sudo rsync' modules/ odroid@odroid-mjmech:/

# prepare new script
ssh odroid@odroid-mjmech
cd /media/boot
dd if=boot-auto_edid.scr bs=1 skip=72 | perl -pe 's/(Image)/$1-at2/g' > /tmp/script
sudo mkimage -T script -d /tmp/script boot-at2.scr
diff -a <(strings boot-auto_edid.scr) <(strings boot-at2.scr)

# reboot and choose new script to test

# switch to serial port @115200
reboot
# Hold "Enter" until you get 'Exynos4412 #' prompt:
fatload mmc 0:1 40008000 boot-at2.scr; run bootscript

# activate new script permanently
cd /media/boot
sudo cp boot-at2.scr boot.scr

-----------------------------
Add rtl8812au (small Edimax wifi dongle):

cd /local2/odroid2
git clone https://github.com/gnab/rtl8812au.git
cd rtl8812au
make ARCH=arm CROSS_COMPILE=$odroid_tc KSRC=../linux
rsync -av --no-owner --no-group --rsync-path='sudo rsync' 8812au.ko odroid@odroid-mjmech:/lib/modules/3.8.13.30-at2/kernel/
ssh odroid@odroid-mjmech sudo depmod -a
# or: ssh odroid@odroid-mjmech -t sudo rmmod 8812au\; sleep 2\; sudo modprobe -v 8812au

-----------------------------
Add mt7619u (small AC600 wifi dongle, really UW-600M01 model):

# note: this only builds driver which does station mode. for AP mode, use make
# parameter MODE=AP to build a different driver.

# note: docs/ contain some documentation. Most of it is extremelty out-of-date
# and seems to be incompatible with current driver (none of the iwpriv names
# match, for example)

cd /local2/odroid2
git clone https://github.com/coolshou/mt7610u
cd mt7610u
make ARCH=arm CROSS_COMPILE=$odroid_tc LINUX_SRC=../linux
rsync -av --no-owner --no-group --rsync-path='sudo rsync' ./os/linux/mt7610u_sta.ko odroid@odroid-mjmech:/lib/modules/3.8.13.30-at2/kernel/
ssh odroid@odroid-mjmech sudo depmod -a '&&' sudo mkdir -p /etc/Wireless/RT2870STA/
rsync -av --no-owner --no-group --rsync-path='sudo rsync' conf/RT2870STA.dat odroid@odroid-mjmech:/etc/Wireless/RT2870STA/

# then add 'coherent_pool=2M' to the end of kernel commandline

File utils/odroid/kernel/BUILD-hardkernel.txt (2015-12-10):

Compiling new odroid kernel
(modified version, from hardkernel)

STATUS: Unsuccessful -- kernel fails to boot
(silence after 'Starting kernel...' message)

-----------------------------
Motivation:

The linux kernel in the odroid distribution we are using is based on 3.8.13.30
kernel modified by hardkernel. This has two problems:
(1) there is no 'build' directory, so it is impossible to build out-of-tree
drivers.
(2) some wireless drivers are too old (such as rt2800usb)

I wanted to do mainline version but I could not get it to work. So here are
the instructions to use patched kernel.

Stock kernel info:
uname: 3.8.13.30 #1 SMP PREEMPT Fri Sep 4 23:45:57 BRT 2015 armv7l armv7l armv7l GNU/Linux
vermagic (from modinfo): 3.8.13.30 SMP preempt mod_unload ARMv7 p2v8
ABI ('file' on module): 32-bit LSB relocatable, ARM, EABI5 version 1 (SYSV)
source: git clone https://github.com/hardkernel/linux.git -b odroid-3.8.y

Instructions:
https://mescanef.net/blog/2014/12/custom-kernel-compilation-for-odroid-u2-u3-on-host-running-fedora-linux/

https://github.com/tobiasjakobi/linux-odroid/archive/odroid-4.3.y.zip

-----------------------------
Preparation:
If you had custom u-boot for mainline kernel, downgrade it with
/usr/local/sbin/odroid-utility.sh
-----------------------------
Process:
We do a cross-compile on a x86_64 machine.

(1) download the kernel, prepare the build dir
 sudo apt-get install gcc-4.7-arm-linux-gnueabi gcc-arm-linux-gnueabi u-boot-tools
 # the kernels are extracted as root, and thus read-only. make the build dir.
 sudo install -d -o $UID /usr/src/kernel-odroid

(1a) get the hardkernel's custom kernel:
 cd /tmp
 wget https://github.com/tobiasjakobi/linux-odroid/archive/odroid-4.3.y.tar.gz
 sudo tar xf odroid-4.3.y -C /usr/src/
 sudo mv /usr/src/linux-odroid-odroid-4.3.y /usr/src/odroid-4.3.y
 # note: 4.3 does not compile with an error:
 #    /usr/src/odroid-4.3.y/drivers/gpu/arm/mali/Kbuild:37: *** Runtime PM is incompatible with non-GPL license.  Stop.

 # patch kernel to remove broken check (I suspect it is not compatible with out-of-tree building)
 sudo nano -w /usr/src/odroid-4.3.y/drivers/gpu/arm/mali/Kbuild
 # replace
 #  ifeq ($(wildcard $(src)/linux/license/gpl/*),)
 # with
 #  ifeq ($(wildcard $(src)/linux/license/gpl/*),NO)

(1b) to get earlier hardkernel default config
 cd /tmp
 wget https://github.com/hardkernel/linux/archive/odroid-3.14.y-linaro.tar.gz
 sudo tar xf odroid-3.14.y-linaro -C /usr/src/
 sudo mv /usr/src/linux-odroid-3.14.y-linaro /usr/src/odroid-3.14.y-ln

(2) configure kernel:
note: always use 'kmake.sh' instead of make in kernel dir, or you many get
options related to x86 kernel. It also move .config file location inside
the tree, so 'git diff' becomes more helpful.

(2a) newer kernel
 tools/odroid/kernel/kmake.sh odroid-4.3.y exynos_defconfig
 tools/odroid/kernel/kmake.sh odroid-4.3.y menuconfig
 # pay attention to options with '(NEW)'
 # make sure to clear CONFIG_EXTRA_FIRMWARE if using mainline kernels
 # make sure to CONFIG_MODULE_COMPRESS is not set

(2b) older kernel

(3) build and copy kernel
 time tools/odroid/kernel/kmake.sh odroid-4.3.y -j4 zImage modules dtbs
 tools/odroid/kernel/kmake.sh odroid-4.3.y modules_install firmware_install zinstall

 # copy all files over to main storage
 rsync -av --rsync-path='sudo rsync' /usr/src/kernel-odroid/odroid-4.3.y-install/ odroid@odroid-mjmech:/

 # copy to /boot partition, on mjmech run:
   cd /media/boot/
   sudo cp /boot/k-4.3.0-mjodroid* .
   head k-4.3.0-mjodroid.script
   # run line from comments
   sudo mkimage -T script -d k-4.3.0-mjodroid.script k-4.3.0-mjodroid.scr

(4) activate the new kernel
 odroid@odroid-mjmech# sudo cp k-4.3.0-mjodroid.scr boot.scr
 odroid@odroid-mjmech# sudo reboot
 (or reboot once and choo

--------
recovery procedure
- connect serial port, open at 115200
- press any key during countdown
- run the original boot script (old bootloader)
fatload mmc 0:1 40008000 boot-auto_edid.scr
run bootscript
# if the bootloader has been updated, the last step will fail; in this case, run:
bootz  0x40008000 0x42000000

- once booted, restore original script:
odroid@odroid-mjmech$ cd /media/boot
odroid@odroid-mjmech$ sudo cp boot-auto_edid.scr boot.scr
odroid@odroid-mjmech$ sudo /usr/local/bin/odroid-utility.sh
# select 'update bootloader'

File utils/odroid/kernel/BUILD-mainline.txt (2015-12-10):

Compiling mainline kernel for odroid

STATUS: Unsuccessful -- kernel fails to boot
(silence after 'Starting kernel...' message)

-----------------------------
Motivation:

The linux kernel in the odroid distribution we are using is based on 3.8.13.30
kernel modified by hardkernel. This has two problems:
(1) there is no 'build' directory, so it is impossible to build out-of-tree
drivers.
(2) some wireless drivers are too old (such as rt2800usb)

There are some instructions on how to partially rebuild a kernel to fix (1),
but if we are going to make our own kernel, we migh t as well go to mainline.

Stock kernel info:
uname: 3.8.13.30 #1 SMP PREEMPT Fri Sep 4 23:45:57 BRT 2015 armv7l armv7l armv7l GNU/Linux
vermagic (from modinfo): 3.8.13.30 SMP preempt mod_unload ARMv7 p2v8
ABI ('file' on module): 32-bit LSB relocatable, ARM, EABI5 version 1 (SYSV)
source: git clone https://github.com/hardkernel/linux.git -b odroid-3.8.y

Inspiration:
http://rglinuxtech.com/?p=1622 (and other posts on this blog)

Instructions:
https://mescanef.net/blog/2014/12/custom-kernel-compilation-for-odroid-u2-u3-on-host-running-fedora-linux/
http://rtisat.blogspot.com/search/label/odroid-u3

-----------------------------
Preparation:
possibly "mainline kernels need an updated u-boot to successfully boot."
http://rtisat.blogspot.com/2015/04/a-little-progress.html

I updated the u-boot via odroid-utility.sh

luckily, initrd does not seem to contain any kernel modules.
check with:
dd bs=64 skip=1 if=/media/boot/uInitrd  | zcat | cpio --list | less

New kernel needs new u-boot, which can be updated per blog post above.
Run the following on the odroid:
    apt-get install device-tree-compiler
    git clone https://github.com/tobiasjakobi/u-boot
    cd u-boot
    make odroid_config
    make
    # commands and constants are from /usr/local/bin/kernel_update.sh
    echo 0 | sudo tee /sys/block/mmcblk0boot0/force_ro
    sudo dd iflag=dsync oflag=dsync if=./u-boot-dtb.bin of=/dev/mmcblk0boot0 seek=62

-----------------------------
Process:
We do a cross-compile on a x86_64 machine.

(1) download the kernel, prepare the build dir
 sudo apt-get install gcc-4.7-arm-linux-gnueabi gcc-arm-linux-gnueabi
 # the kernels are extracted as root, and thus read-only. make the build dir.
 sudo install -d -o $UID /usr/src/kernel-odroid

(1a) get the stock kernel. note
 cd /tmp
 wget https://cdn.kernel.org/pub/linux/kernel/v4.x/linux-4.3.tar.xz
 sudo tar xJf linux-4.3.tar.xz -C /usr/src
  get the odroid kernel

(2) configure kernel:
note: always use 'kmake.sh' instead of make in kernel dir, or you many get
options related to x86 kernel. It also move .config file location inside
the tree, so 'git diff' becomes more helpful.

use previous configuration with new things set as modules:
 rm tools/odroid/kernel/config-linux-4.3
 KCONFIG_ALLCONFIG=$PWD/tools/odroid/kernel/config-hardkernel-3.8.13.30 \
     tools/odroid/kernel/kmake.sh linux-4.3 allmodconfig
OR use previous configuration with new things set as default:
 cp tools/odroid/kernel/config-hardkernel-3.8.13.30 tools/odroid/kernel/config-linux-4.3
 tools/odroid/kernel/kmake.sh linux-4.3 olddefconfig

the enter/exit menunconfig to inspect it by hand and update the config:
 tools/odroid/kernel/kmake.sh linux-4.3 menuconfig
 # pay attention to options with '(NEW)'
 # make sure to clear CONFIG_EXTRA_FIRMWARE if using mainline kernels
 # make sure to CONFIG_MODULE_COMPRESS is not set

(3) build and copy modules
 time tools/odroid/kernel/kmake.sh linux-4.3 -j4 zImage modules
 tools/odroid/kernel/kmake.sh linux-4.3 modules_install firmware_install zinstall

 # Check version
 tools/odroid/kernel/kmake.sh linux-4.3 -s kernelrelease
 # optionally delete old modules
 rm /usr/src/kernel-odroid/linux-4.3-install/boot/*.old
 ssh odroid@odroid-mjmech rm -rf /lib/modules/4.3.0-mjmech1 /lib/firmware-linux-4.3
 # copy all files over (this will not activate them yet)
 rsync -av --rsync-path='sudo rsync' /usr/src/kernel-odroid/linux-4.3-install/ odroid@odroid-mjmech:/

 # copy to /boot partition
 odroid@odroid-mjmech# sudo cp /boot/exynos4412-odroidu3.dtb /media/boot/
 odroid@odroid-mjmech# sudo cp /boot/vmlinuz-4.3.0-mjmech1 /media/boot/zImage-4.3
 sudo mkimage -T script -d kernel-4.3.script kernel-4.3.scr

(4) activate the new kernel
 odroid@odroid-mjmech# sudo cp kernel-4.3.scr boot.scr
 odroid@odroid-mjmech# sudo reboot

--------
recovery procedure
- connect serial port, open at 115200
- press any key during countdown
- run the original boot script (old bootloader)
fatload mmc 0:1 40008000 boot-auto_edid.scr
run bootscript
# if the bootloader has been updated, the last step will fail; in this case, run:
bootz  0x40008000 0x42000000

- once booted, restore original script:
odroid@odroid-mjmech$ cd /media/boot
odroid@odroid-mjmech$ sudo cp boot-auto_edid.scr boot.scr
odroid@odroid-mjmech$ sudo /usr/local/bin/odroid-utility.sh
# select 'update bootloader'

- examine the current config (or just see the boot.scr file on original image)
Exynos4412 # printenv bootcmd
bootcmd=    cfgload; mmc rescan 0:1; mmc rescan 0:2;  if run loadbootscript_1;     then run bootscript;  else     if run loadbootscript_2;  |
Exynos4412 # cfgload
do_fat_cfgload : cmd = fatload mmc 0:1 0x41000000 boot.ini
reading boot.ini
** Unable to read file boot.ini **
Exynos4412 # printenv loadbootscript_1
loadbootscript_1=echo >>> Load Boot Script from mmc 0:1 <<<;fatload mmc 0:1 40008000 boot.scr
Exynos4412 # run loadbootscript_1
>>> Load Boot Script from mmc 0:1 <<<
reading boot.scr
Warning : Reads a file that is smaller than the cluster size.
380 bytes read in 34 ms (10.7 KiB/s)
Exynos4412 # printenv bootscript
bootscript=source 40008000
Exynos4412 # md 40008000 75
40008000: 56190527 379fda4f 3e2d7d52 3c010000    '..VO..7R}->...<
40008010: 00000000 00000000 39df7f05 00060205    ...........9....
40008020: 746f6f62 7263732e 726f6620 77205820    boot.scr for X w
40008030: 20687469 494d4448 74756120 72702d6f    ith HDMI auto-pr
40008040: 34010000 00000000 65746573 6920766e    ...4....setenv i
40008050: 7274696e 69685f64 22206867 66667830    nitrd_high "0xff

- run stored commands using different kernel name
setenv initrd_high "0xffffffff"
setenv fdt_high "0xffffffff"
setenv bootcmd "fatload mmc 0:1 0x40008000 zImage.0; fatload mmc 0:1 0x42000000 uInitrd; bootm 0x40008000 0x42000000"
setenv edid_load "drm_kms_helper.edid_firmware=edid/1024x768.bin"
setenv bootargs "console=tty1 console=ttySAC1,115200n8 ${edid_load} root=UUID=e139ce78-9841-40fe-8823-96a304a09859 rootwait ro  mem=2047M"
boot

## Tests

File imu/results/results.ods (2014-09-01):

 | rad/sqrt(s)
ARW | 3.00E-005 | 0.0017 | 0.01
Bias Stability | 1.00E-005 | 0.0006
Comparable | max21000
Measurement Noise (mps2) | 1 |  |  |  |  |  | Measurement Noise (mps2) | 10 |  |  |  |  |  | 0.1 |  |  |  |  |  |  | 0.01
Pitch Process (deg/s) | Bias Process deg/sqrt(s) | Pitch uncert (deg) | Bias uncert (deg) |  |  |  | Pitch Process (deg/s) | Bias Process deg/sqrt(s) | Pitch uncert (deg) | Bias uncert (deg) |  |  |  | Pitch Process (deg/s) | Bias Process deg/sqrt(s) | Pitch uncert (deg) | Bias uncert (deg) |  |  |  | Pitch Process (deg/s) | Bias Process deg/sqrt(s) | Pitch uncert (deg) | Bias uncert (deg)
3.2767 | 0.8192 | 5.068 | 1.918 | 0.0923 | 0.0671 | 0.0854 | 3.2767 | 0.8192 |  |  |  |  |  | 0.0008 | 0.01024 | 0.4424 | 0.187 | 0.0798 | 0.0827 | 0.0875 | 0.0008 | 0.01024
0.0008 | 0.0512 | 2.095 | 0.198 | 0.0448 | 0.0375 | 0.0447 | 0.0008 | 0.0512 | 11.945 | 0.349 | 0.0243 | 0.0239 | 0.014 | 0.0008 | 0.0512 | 0.37214 | 0.111 | 0.0747 | 0.0687 | 0.0846 | 0.0008 | 0.0512
0.0008 | 0.0256 | 1.762 | 0.118 | 0.0345 | 0.0461 | 0.033 | 0.0008 | 0.0256 |  |  |  |  |  | 0.0008 | 0.0256 | 0.313 | 0.0662 | 0.0665 | 0.0536 | 0.0687 | 0.0008 | 0.0256
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

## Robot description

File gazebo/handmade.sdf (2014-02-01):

<?xml version="1.0"?>
<sdf version="1.4">
  <model name="mj_mech">
    <static>false</static>

    <link name="chassis">
      <pose>0 0 0.1 0 0 0</pose>
      <inertial><mass>0.4</mass></inertial>
      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
    </link>


    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

    <link name="body_bracket1">
      <pose>0.13 0.1 0.1 0 0 0</pose>
      <inertial><mass>0.05</mass></inertial>
      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
    </link>

    <joint type="revolute" name="body_hinge1">
      <pose>-0.03 0.0 0.0 0 0 0</pose>
      <child>body_bracket1</child>
      <parent>chassis</parent>
      <axis>
        <xyz>0 0 1</xyz>
        <dynamics><damping>0.1</damping><friction>0.2</friction></dynamics>
      </axis>
    </joint>

    <link name="coxa1">
      <pose>0.19 0.1 0.115 0 -0.4 0</pose>
      <inertial><mass>0.05</mass></inertial>
      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
    </link>

    <joint type="revolute" name="coxa_hinge1">
      <pose>-0.03 0.0 0.0 0 0 0</pose>
      <child>coxa1</child>
      <parent>body_bracket1</parent>
      <axis>
        <xyz>0 1 0</xyz>
        <dynamics><damping>0.1</damping><friction>0.2</friction></dynamics>
      </axis>
    </joint>

    <link name="femur1">
      <pose>0.25 0.1 0.095 0 1.0 0</pose>
      <inertial><mass>0.05</mass></inertial>
      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
    </link>

    <joint type="revolute" name="femur_hinge1">
      <pose>-0.03 0.0 0.0 0 0 0</pose>
      <child>femur1</child>
      <parent>coxa1</parent>
      <axis>
        <xyz>0 1 0</xyz>
        <dynamics><damping>0.1</damping><friction>0.2</friction></dynamics>
      </axis>
    </joint>


    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

    <link name="body_bracket2">
      <pose>0.13 -0.1 0.1 0 0 0</pose>
      <inertial><mass>0.05</mass></inertial>
      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
    </link>

    <joint type="revolute" name="body_hinge2">
      <pose>-0.03 0.0 0.0 0 0 0</pose>
      <child>body_bracket2</child>
      <parent>chassis</parent>
      <axis>
        <xyz>0 0 1</xyz>
        <dynamics><damping>0.1</damping><friction>0.2</friction></dynamics>
      </axis>
    </joint>

    <link name="coxa2">
      <pose>0.19 -0.1 0.115 0 -0.4 0</pose>
      <inertial><mass>0.05</mass></inertial>
      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
    </link>

    <joint type="revolute" name="coxa_hinge2">
      <pose>-0.03 0.0 0.0 0 0 0</pose>
      <child>coxa2</child>
      <parent>body_bracket2</parent>
      <axis>
        <xyz>0 1 0</xyz>
        <dynamics><damping>0.1</damping><friction>0.2</friction></dynamics>
      </axis>
    </joint>

    <link name="femur2">
      <pose>0.25 -0.1 0.095 0 1.0 0</pose>
      <inertial><mass>0.05</mass></inertial>
      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
    </link>

    <joint type="revolute" name="femur_hinge2">
      <pose>-0.03 0.0 0.0 0 0 0</pose>
      <child>femur2</child>
      <parent>coxa2</parent>
      <axis>
        <xyz>0 1 0</xyz>
        <dynamics><damping>0.1</damping><friction>0.2</friction></dynamics>
      </axis>
    </joint>

    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

    <link name="body_bracket3">
      <pose>-0.13 0.1 0.1 0 0 3.14159</pose>
      <inertial><mass>0.05</mass></inertial>
      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
    </link>

    <joint type="revolute" name="body_hinge3">
      <pose>-0.03 0.0 0.0 0 0 0</pose>
      <child>body_bracket3</child>
      <parent>chassis</parent>
      <axis>
        <xyz>0 0 1</xyz>
        <dynamics><damping>0.1</damping><friction>0.2</friction></dynamics>
      </axis>
    </joint>

    <link name="coxa3">
      <pose>-0.19 0.1 0.115 0 -0.4 3.14159</pose>
      <inertial><mass>0.05</mass></inertial>
      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
    </link>

    <joint type="revolute" name="coxa_hinge3">
      <pose>-0.03 0.0 0.0 0 0 0</pose>
      <child>coxa3</child>
      <parent>body_bracket3</parent>
      <axis>
        <xyz>0 1 0</xyz>
        <dynamics><damping>0.1</damping><friction>0.2</friction></dynamics>
      </axis>
    </joint>

    <link name="femur3">
      <pose>-0.25 0.1 0.095 0 1.0 3.14159</pose>
      <inertial><mass>0.05</mass></inertial>
      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
    </link>

    <joint type="revolute" name="femur_hinge3">
      <pose>-0.03 0.0 0.0 0 0 0</pose>
      <child>femur3</child>
      <parent>coxa3</parent>
      <axis>
        <xyz>0 1 0</xyz>
        <dynamics><damping>0.1</damping><friction>0.2</friction></dynamics>
      </axis>
    </joint>

    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

    <link name="body_bracket4">
      <pose>-0.13 -0.1 0.1 0 0 3.14159</pose>
      <inertial><mass>0.05</mass></inertial>
      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
    </link>

    <joint type="revolute" name="body_hinge4">
      <pose>-0.03 0.0 0.0 0 0 0</pose>
      <child>body_bracket4</child>
      <parent>chassis</parent>
      <axis>
        <xyz>0 0 1</xyz>
        <dynamics><damping>0.1</damping><friction>0.2</friction></dynamics>
      </axis>
    </joint>

    <link name="coxa4">
      <pose>-0.19 -0.1 0.115 0 -0.4 3.14159</pose>
      <inertial><mass>0.05</mass></inertial>
      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
    </link>

    <joint type="revolute" name="coxa_hinge4">
      <pose>-0.03 0.0 0.0 0 0 0</pose>
      <child>coxa4</child>
      <parent>body_bracket4</parent>
      <axis>
        <xyz>0 1 0</xyz>
        <dynamics><damping>0.1</damping><friction>0.2</friction></dynamics>
      </axis>
    </joint>

    <link name="femur4">
      <pose>-0.25 -0.1 0.095 0 1.0 3.14159</pose>
      <inertial><mass>0.05</mass></inertial>
      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
    </link>

    <joint type="revolute" name="femur_hinge4">
      <pose>-0.03 0.0 0.0 0 0 0</pose>
      <child>femur4</child>
      <parent>coxa4</parent>
      <axis>
        <xyz>0 1 0</xyz>
        <dynamics><damping>0.1</damping><friction>0.2</friction></dynamics>
      </axis>
    </joint>
  </model>
</sdf>

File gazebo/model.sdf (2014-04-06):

<?xml version="1.0"?>
<sdf version="1.4">
  <model name="mj_mech">
    <static>false</static>



    <link name="chassis">
      <pose>0 0 0.400000 0 0 0</pose>
      <inertial>
        <mass>1.050000</mass>
        <inertia>
          <ixx>0.015162</ixx>
          <ixy>0.00</ixy>
          <ixz>0.00</ixz>
          <iyy>0.015162</iyy>
          <iyz>0.00</iyz>
          <izz>0.015162</izz>
        </inertia>
      </inertial>
      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
    </link>


    <link name="pan_aeg">
      <pose>0.000000 0.010000 0.459000 0.000000 0.000000 0.000000</pose>
      <inertial>
        <mass>0.100000</mass>
        <inertia>
          <ixx>0.000160</ixx>
          <ixy>0.00</ixy>
          <ixz>0.00</ixz>
          <iyy>0.000160</iyy>
          <iyz>0.00</iyz>
          <izz>0.000160</izz>
        </inertia>
      </inertial>
      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
    </link>


    <joint type="revolute" name="pan_aeg_hinge">
      <pose>0.000000 0.000000 0.000000 0 0 0</pose>
      <child>pan_aeg</child>
      <parent>chassis</parent>
      <axis>
        <xyz>0.000000 0.000000 1.000000</xyz>
        <dynamics><damping>0.1</damping><friction>0.1</friction></dynamics>
        <limit>
          <effort>1.200000</effort>
          <velocity>3.0</velocity>
        </limit>
      </axis>
    </joint>


    <link name="weapon_assembly">
      <pose>0.000000 0.010000 0.479000 0.000000 0.000000 0.000000</pose>
      <inertial>
        <mass>0.550000</mass>
        <inertia>
          <ixx>0.026400</ixx>
          <ixy>0.00</ixy>
          <ixz>0.00</ixz>
          <iyy>0.026400</iyy>
          <iyz>0.00</iyz>
          <izz>0.026400</izz>
        </inertia>
      </inertial>
      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
    </link>


    <joint type="revolute" name="weapon_assembly_hinge">
      <pose>0.000000 0.000000 0.000000 0 0 0</pose>
      <child>weapon_assembly</child>
      <parent>pan_aeg</parent>
      <axis>
        <xyz>1.000000 0.000000 0.000000</xyz>
        <dynamics><damping>0.1</damping><friction>0.1</friction></dynamics>
        <limit>
          <effort>1.200000</effort>
          <velocity>3.0</velocity>
        </limit>
      </axis>
    </joint>


    <link name="coxa0">
      <pose>0.100000 0.081000 0.411000 0.000000 0.000000 0.000000</pose>
      <inertial>
        <mass>0.067000</mass>
        <inertia>
          <ixx>0.000965</ixx>
          <ixy>0.00</ixy>
          <ixz>0.00</ixz>
          <iyy>0.000965</iyy>
          <iyz>0.00</iyz>
          <izz>0.000965</izz>
        </inertia>
      </inertial>
      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
    </link>


    <joint type="revolute" name="coxa_hinge0">
      <pose>0.000000 0.000000 0.000000 0 0 0</pose>
      <child>coxa0</child>
      <parent>chassis</parent>
      <axis>
        <xyz>0.000000 0.000000 1.000000</xyz>
        <dynamics><damping>0.1</damping><friction>0.1</friction></dynamics>
        <limit>
          <effort>1.200000</effort>
          <velocity>3.0</velocity>
        </limit>
      </axis>
    </joint>


    <link name="femur0">
      <pose>0.160000 0.081000 0.411000 0.000000 0.000000 0.000000</pose>
      <inertial>
        <mass>0.067000</mass>
        <inertia>
          <ixx>0.000965</ixx>
          <ixy>0.00</ixy>
          <ixz>0.00</ixz>
          <iyy>0.000965</iyy>
          <iyz>0.00</iyz>
          <izz>0.000965</izz>
        </inertia>
      </inertial>
      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
    </link>


    <joint type="revolute" name="femur_hinge0">
      <pose>0.000000 0.000000 0.000000 0 0 0</pose>
      <child>femur0</child>
      <parent>coxa0</parent>
      <axis>
        <xyz>0.000000 1.000000 0.000000</xyz>
        <dynamics><damping>0.1</damping><friction>0.1</friction></dynamics>
        <limit>
          <effort>1.200000</effort>
          <velocity>3.0</velocity>
        </limit>
      </axis>
    </joint>


    <link name="tibia0">
      <pose>0.220000 0.081000 0.411000 0.000000 0.000000 0.000000</pose>
      <inertial>
        <mass>0.067000</mass>
        <inertia>
          <ixx>0.000965</ixx>
          <ixy>0.00</ixy>
          <ixz>0.00</ixz>
          <iyy>0.000965</iyy>
          <iyz>0.00</iyz>
          <izz>0.000965</izz>
        </inertia>
      </inertial>
      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
    </link>


    <joint type="revolute" name="tibia_hinge0">
      <pose>0.000000 0.000000 0.000000 0 0 0</pose>
      <child>tibia0</child>
      <parent>femur0</parent>
      <axis>
        <xyz>0.000000 1.000000 0.000000</xyz>
        <dynamics><damping>0.1</damping><friction>0.1</friction></dynamics>
        <limit>
          <effort>1.200000</effort>
          <velocity>3.0</velocity>
        </limit>
      </axis>
    </joint>


    <link name="tip0">
      <pose>0.280000 0.081000 0.411000 0 0 0</pose>
      <inertial>
        <mass>0.020000</mass>
        <inertia>
          <ixx>0.000002</ixx>
          <ixy>0.00</ixy>
          <ixz>0.00</ixz>
          <iyy>0.000002</iyy>
          <iyz>0.00</iyz>
          <izz>0.000002</izz>
        </inertia>
      </inertial>
      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
    </link>


    <joint type="revolute" name="tip_hinge0">
      <pose>0.000000 0.000000 0.000000 0 0 0</pose>
      <child>tip0</child>
      <parent>tibia0</parent>
      <axis>
        <xyz>1 0 0</xyz>
        <limit>
          <upper>0</upper>
          <lower>0</lower>
        </limit>
        <dynamics><damping>0.1</damping><friction>0.1</friction></dynamics>
      </axis>
    </joint>


    <link name="coxa1">
      <pose>0.100000 -0.081000 0.411000 0.000000 0.000000 0.000000</pose>
      <inertial>
        <mass>0.067000</mass>
        <inertia>
          <ixx>0.000965</ixx>
          <ixy>0.00</ixy>
          <ixz>0.00</ixz>
          <iyy>0.000965</iyy>
          <iyz>0.00</iyz>
          <izz>0.000965</izz>
        </inertia>
      </inertial>
      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
    </link>


    <joint type="revolute" name="coxa_hinge1">
      <pose>0.000000 0.000000 0.000000 0 0 0</pose>
      <child>coxa1</child>
      <parent>chassis</parent>
      <axis>
        <xyz>0.000000 0.000000 1.000000</xyz>
        <dynamics><damping>0.1</damping><friction>0.1</friction></dynamics>
        <limit>
          <effort>1.200000</effort>
          <velocity>3.0</velocity>
        </limit>
      </axis>
    </joint>


    <link name="femur1">
      <pose>0.160000 -0.081000 0.411000 0.000000 0.000000 0.000000</pose>
      <inertial>
        <mass>0.067000</mass>
        <inertia>
          <ixx>0.000965</ixx>
          <ixy>0.00</ixy>
          <ixz>0.00</ixz>
          <iyy>0.000965</iyy>
          <iyz>0.00</iyz>
          <izz>0.000965</izz>
        </inertia>
      </inertial>
      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
    </link>
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

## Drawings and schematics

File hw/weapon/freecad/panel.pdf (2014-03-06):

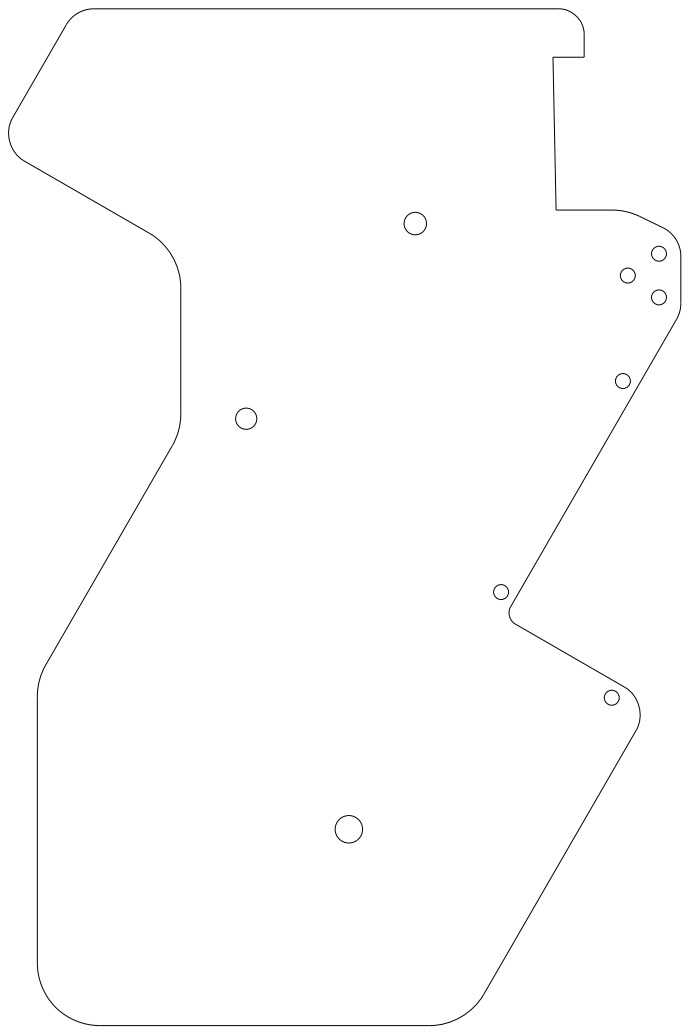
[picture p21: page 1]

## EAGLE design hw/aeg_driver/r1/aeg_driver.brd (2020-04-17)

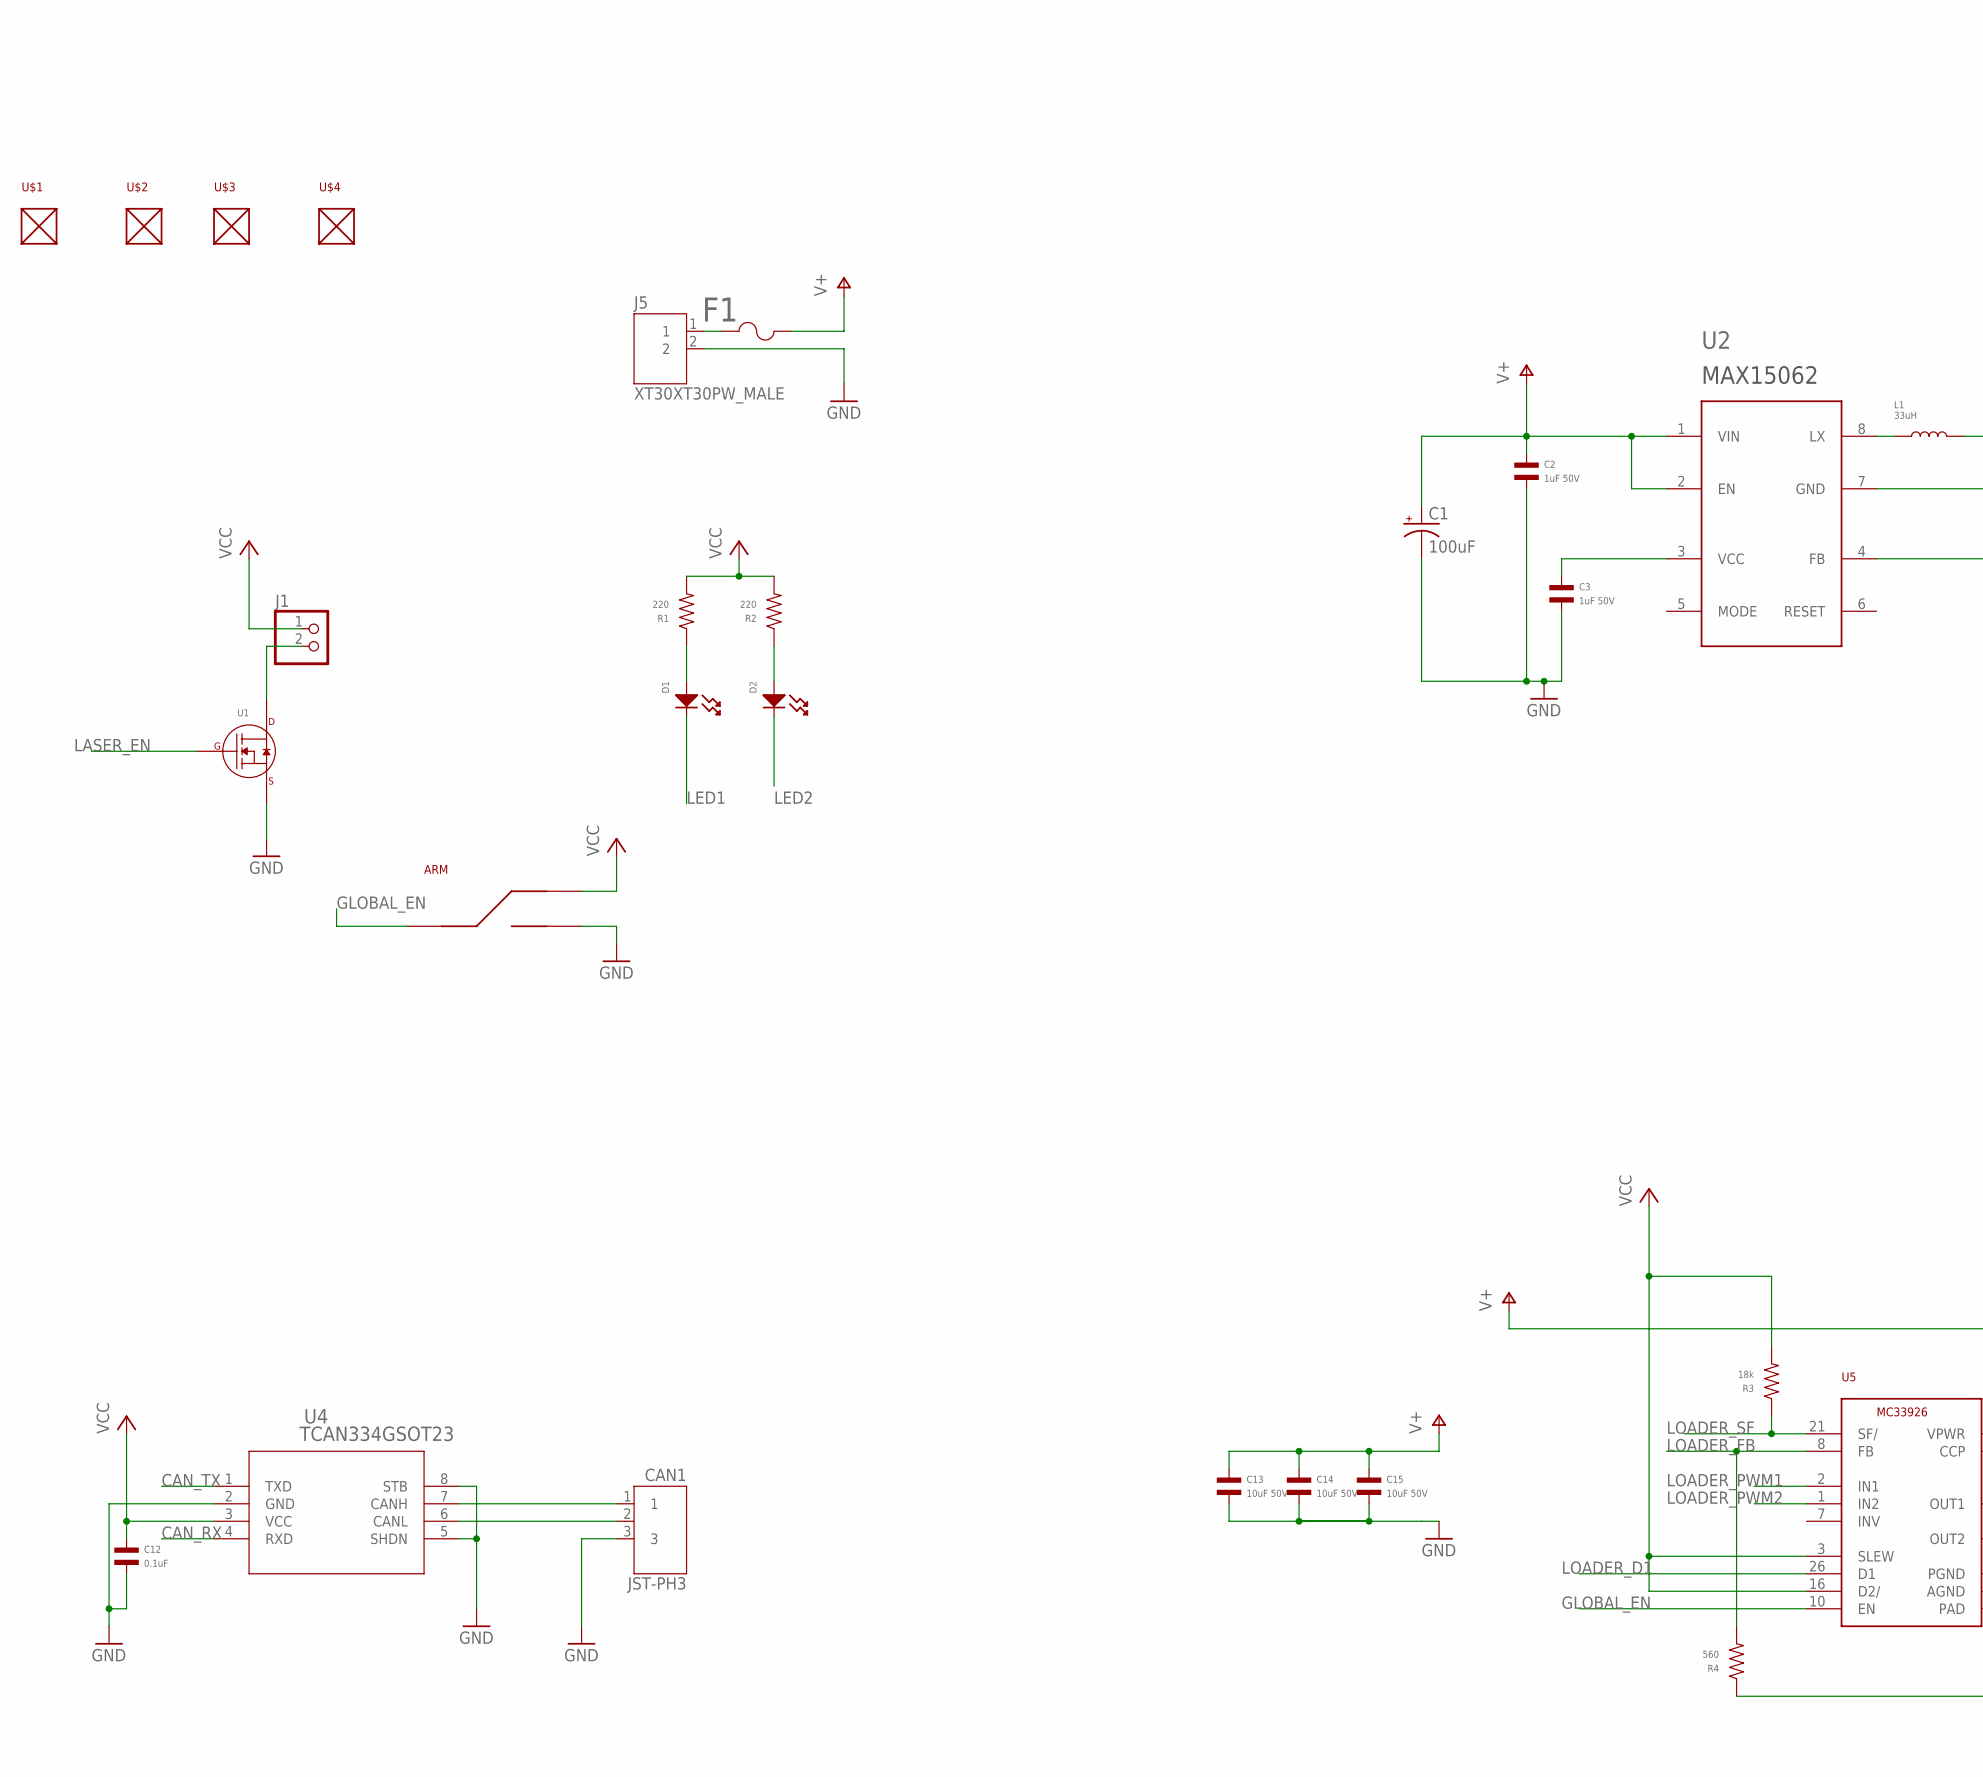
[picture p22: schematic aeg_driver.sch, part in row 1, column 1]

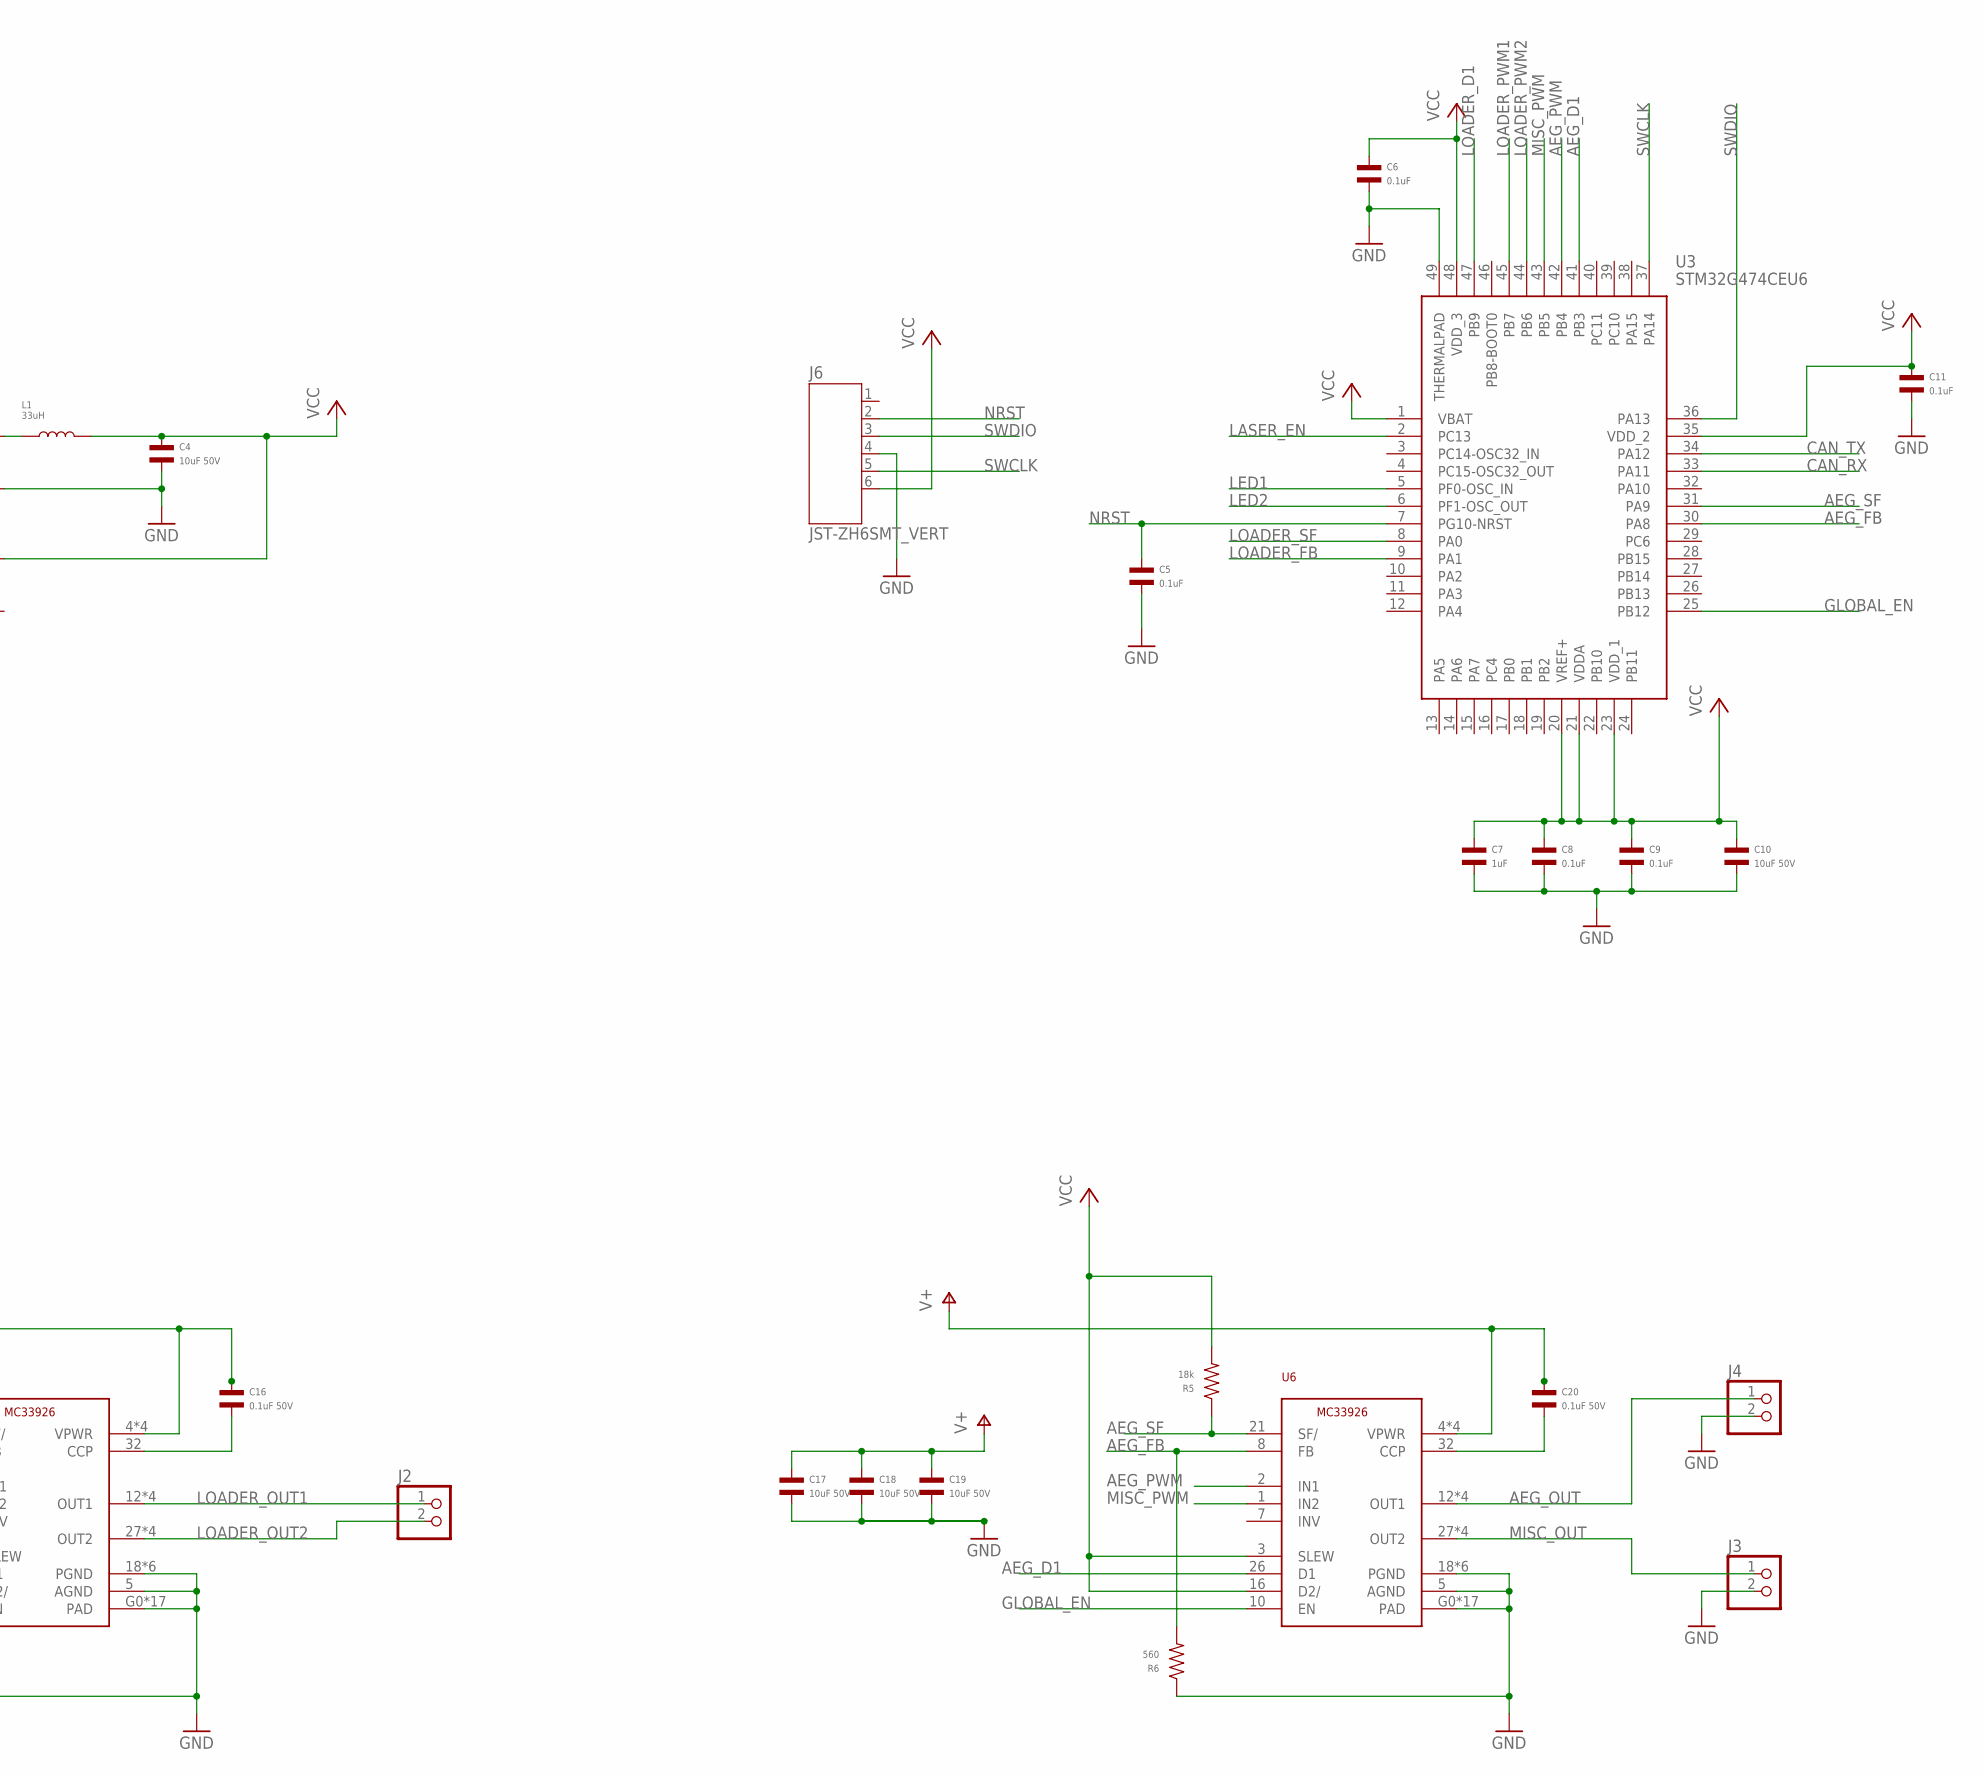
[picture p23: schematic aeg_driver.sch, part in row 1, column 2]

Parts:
ARM: SLIDE_SWITCHJS_SUB_SWITCH; JS_SUB_SWITCH; MPN JS102011SAQN
C1: 100uF; PANASONIC_FT_CAP_D; MPN EEE-FT1V101AP
C2, C3: 1uF 50V; C0603; MPN CL10A105KB8NNNC
C4, C10, C13, C14, C15, C17, C18, C19: 10uF 50V; C1206; MPN C3216X7R1H106K160AE
C5, C6, C8, C9, C11, C12: 0.1uF; C0402; MPN MF-CAP-0402-0.1uF
C7: 1uF; C0402; MPN MF-CAP-0402-1uF
C16, C20: 0.1uF 50V; C0402; MPN 0402B104K500CT
CAN1: JST-PH3; JST_S3B-PH-SM4-TB(LF)(SN); MPN S3B-PH-SM4-TB(LF)(SN)
D1: LED_SINGLE-0603-RED; LED0603
D2: LED_SINGLE-0603-RED; LED0603; MPN MF-LED-0603-GREEN
F1: MFU0603FF04000P100; FUS_VISHAY_MFU0603; MPN MFU0603FF04000P100
J1, J2, J3, J4: PINHD-1X2; 1X02
J5: XT30XT30PW_MALE; XT30PW_MALE; MPN XT30PW-M
J6: JST-ZH6SMT_VERT; JST_B6B-ZR-SM4-TF(LF)(SN); MPN B6B-ZR-SM4-TF(LF)(SN)
L1: 33uH; L1210; MPN NLFV32T-330K-EF
R1, R2: 220; R0603; MPN MF-RES-0603-220
R3, R5: 18k; R0603; MPN MF-RES-0603-18K
R4, R6: 560; R0603; MPN MF-RES-0603-560
U1: N-CHANNEL_FET_SOT-23-3; SOT-23-3; MPN MF-DSC-SOT233-BSS138
U2: MAX150628TDFN; 8TDFN; MPN MAX15062AATA+T
U3: STM32G474CEU6; QFN50P700X700X60-49N; MPN STM32G474CEU6
U4: TCAN334GSOT23; SOT23-8; MPN TCAN334GDCNT
U5, U6: MC33926; PQFN32; MPN MC33926PNBR2
U$1, U$2, U$3, U$4: MOUNT; M2.5MOUNT

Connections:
AEG_D1: U3.41 (PB3), U6.26 (D1)
AEG_FB: R6.P$2, U3.30 (PA8), U6.8 (FB)
AEG_OUT: J4.1, U6.12 (OUT1), U6.13 (OUT1), U6.14 (OUT1), U6.15 (OUT1)
AEG_PWM: U3.42 (PB4), U6.2 (IN1)
AEG_SF: R5.P$1, U3.31 (PA9), U6.21 (SF/)
CAN_N: CAN1.2, U4.6 (CANL)
CAN_P: CAN1.1, U4.7 (CANH)
CAN_RX: U3.33 (PA11), U4.4 (RXD)
CAN_TX: U3.34 (PA12), U4.1 (TXD)
GLOBAL_EN: ARM.2, U3.25 (PB12), U5.10 (EN), U6.10 (EN)
GND: ARM.3, C1.-, C2.P$2, C3.P$2, C4.P$2, C5.P$2, C6.P$2, C7.P$2, C8.P$2, C9.P$2, C10.P$2, C11.P$2, C12.P$2, C13.P$2, C14.P$2, C15.P$2, C17.P$2, C18.P$2, C19.P$2, CAN1.3, J3.2, J4.2, J5.2, J6.4, R4.P$1, R6.P$1, U1.P$2 (SOURCE), U2.7 (GND), U3.49 (THERMALPAD), U4.2 (GND), U4.5 (SHDN), U4.8 (STB), U5.5 (AGND), U5.18 (PGND), U5.19 (PGND), U5.20 (PGND), U5.22 (PGND), U5.23 (PGND), U5.24 (PGND), U5.G0 (PAD), U5.G1 (PAD), U5.G2 (PAD), U5.G3 (PAD), U5.G4 (PAD), U5.G5 (PAD), U5.G6 (PAD), U5.G7 (PAD), U5.G8 (PAD), U5.G9 (PAD), U5.G10 (PAD), U5.G11 (PAD), U5.G12 (PAD), U5.G13 (PAD), U5.G14 (PAD), U5.G15 (PAD), U5.G16 (PAD), U6.5 (AGND), U6.18 (PGND), U6.19 (PGND), U6.20 (PGND), U6.22 (PGND), U6.23 (PGND), U6.24 (PGND), U6.G0 (PAD), U6.G1 (PAD), U6.G2 (PAD), U6.G3 (PAD), U6.G4 (PAD), U6.G5 (PAD), U6.G6 (PAD), U6.G7 (PAD), U6.G8 (PAD), U6.G9 (PAD), U6.G10 (PAD), U6.G11 (PAD), U6.G12 (PAD), U6.G13 (PAD), U6.G14 (PAD), U6.G15 (PAD), U6.G16 (PAD)
LASER_EN: U1.P$1 (GATE), U3.2 (PC13)
LED1: D1.CATHODE, U3.5 (PF0-OSC_IN)
LED2: D2.CATHODE, U3.6 (PF1-OSC_OUT)
LOADER_D1: U3.47 (PB9), U5.26 (D1)
LOADER_FB: R4.P$2, U3.9 (PA1), U5.8 (FB)
LOADER_OUT1: J2.1, U5.12 (OUT1), U5.13 (OUT1), U5.14 (OUT1), U5.15 (OUT1)
LOADER_OUT2: J2.2, U5.27 (OUT2), U5.28 (OUT2), U5.29 (OUT2), U5.30 (OUT2)
LOADER_PWM1: U3.45 (PB7), U5.2 (IN1)
LOADER_PWM2: U3.44 (PB6), U5.1 (IN2)
LOADER_SF: R3.P$1, U3.8 (PA0), U5.21 (SF/)
LX: L1.P$1, U2.8 (LX)
MISC_OUT: J3.1, U6.27 (OUT2), U6.28 (OUT2), U6.29 (OUT2), U6.30 (OUT2)
MISC_PWM: U3.43 (PB5), U6.1 (IN2)
unnamed: C20.P$2, U6.32 (CCP)
unnamed: J1.2, U1.P$3 (DRAIN)
unnamed: F1.1, J5.1
unnamed: C16.P$2, U5.32 (CCP)
unnamed: C3.P$1, U2.3 (VCC)
unnamed: D1.ANODE, R1.P$1
unnamed: D2.ANODE, R2.P$1
NRST: C5.P$1, J6.2, U3.7 (PG10-NRST)
SWCLK: J6.5, U3.37 (PA14)
SWDIO: J6.3, U3.36 (PA13)
V+: C1.+, C2.P$1, C13.P$1, C14.P$1, C15.P$1, C16.P$1, C17.P$1, C18.P$1, C19.P$1, C20.P$1, F1.2, U2.1 (VIN), U2.2 (EN), U5.4 (VPWR), U5.6 (VPWR), U5.11 (VPWR), U5.31 (VPWR), U6.4 (VPWR), U6.6 (VPWR), U6.11 (VPWR), U6.31 (VPWR)
VCC: ARM.1, C4.P$1, C6.P$1, C7.P$1, C8.P$1, C9.P$1, C10.P$1, C11.P$1, C12.P$1, J1.1, J6.6, L1.P$2, R1.P$2, R2.P$2, R3.P$2, R5.P$2, U2.4 (FB), U3.1 (VBAT), U3.20 (VREF+), U3.21 (VDDA), U3.23 (VDD_1), U3.35 (VDD_2), U3.48 (VDD_3), U4.3 (VCC), U5.3 (SLEW), U5.16 (D2/), U6.3 (SLEW), U6.16 (D2/)

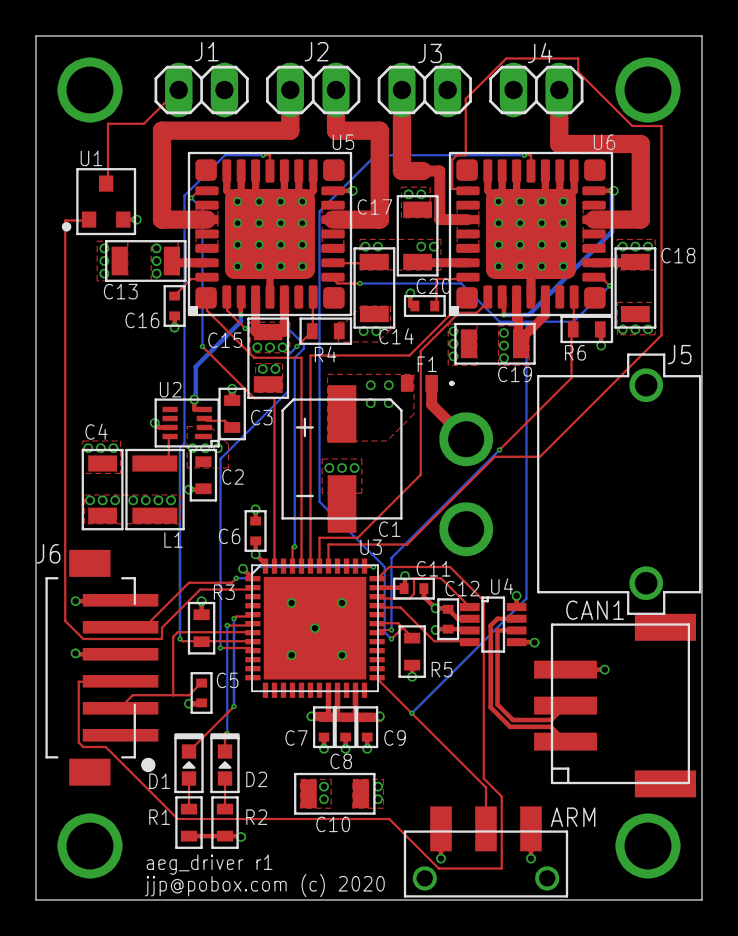
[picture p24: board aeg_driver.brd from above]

Board: 4 copper layers, 37.0 x 48.0 mm, 48 parts (0 on the bottom side), 36 nets.

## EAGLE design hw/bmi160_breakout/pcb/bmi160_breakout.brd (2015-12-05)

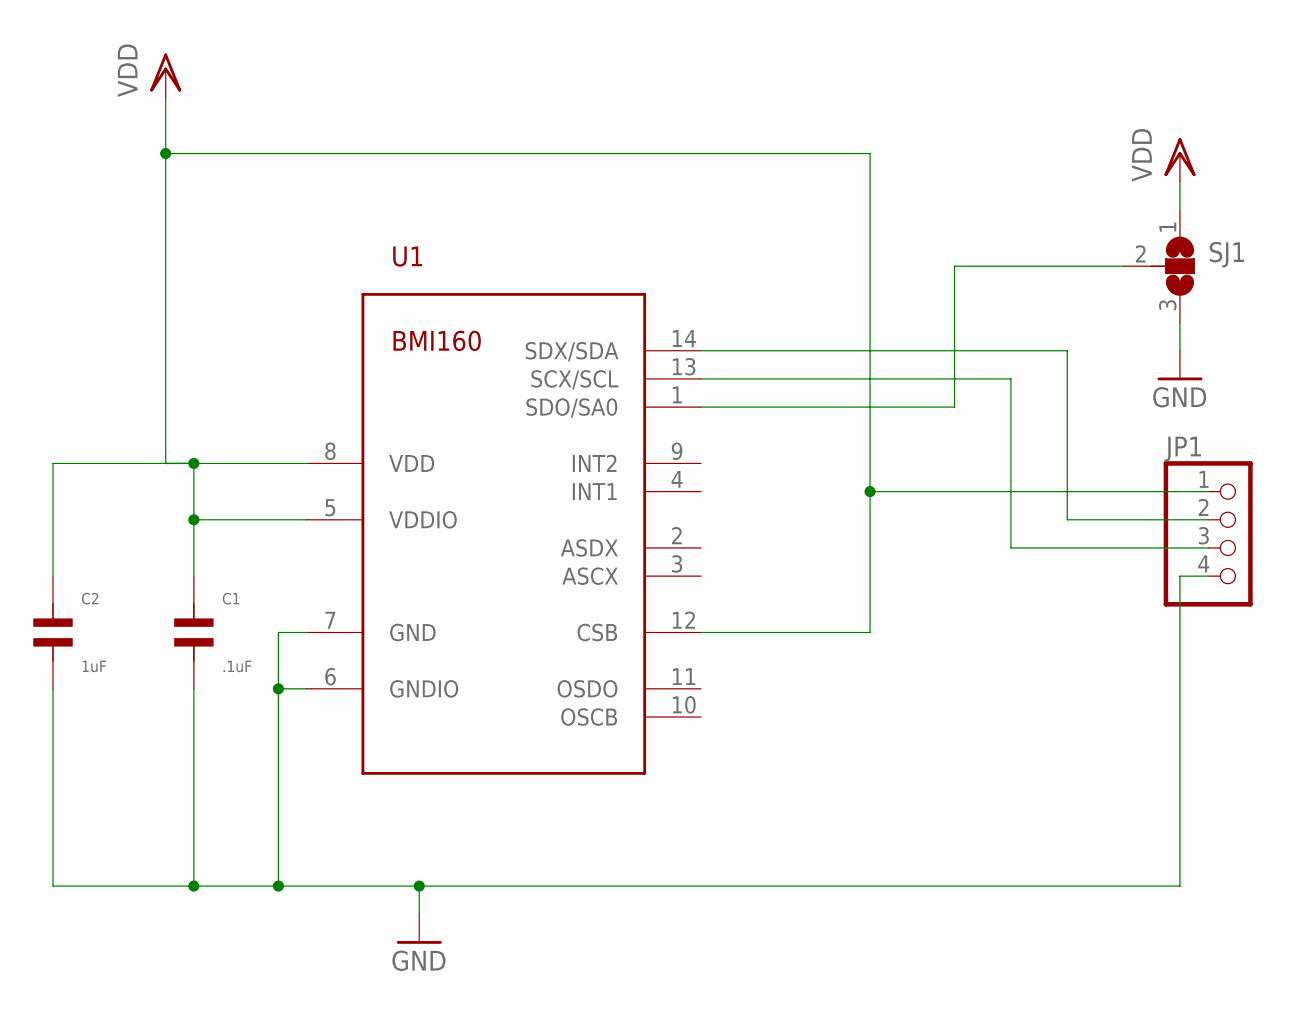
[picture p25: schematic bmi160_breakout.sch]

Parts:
C1: .1uF; C0603
C2: 1uF; C0805
JP1: PINHD-1X4; 1X04
SJ1: SJ2W; SJ_2
U1: BMI160LGA14; LGA14; MOUSER_PN 262-BMI160

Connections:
GND: C1.P$2, C2.P$2, JP1.4, SJ1.3, U1.6 (GNDIO), U1.7 (GND)
unnamed: SJ1.2, U1.1 (SDO/SA0)
SCL: JP1.3, U1.13 (SCX/SCL)
SDA: JP1.2, U1.14 (SDX/SDA)
VDD: C1.P$1, C2.P$1, JP1.1, SJ1.1, U1.5 (VDDIO), U1.8 (VDD), U1.12 (CSB)

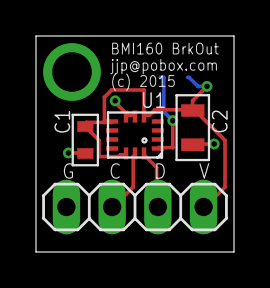
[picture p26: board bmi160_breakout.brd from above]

Board: 2 copper layers, 11.0 x 12.0 mm, 5 parts (1 on the bottom side), 5 nets.

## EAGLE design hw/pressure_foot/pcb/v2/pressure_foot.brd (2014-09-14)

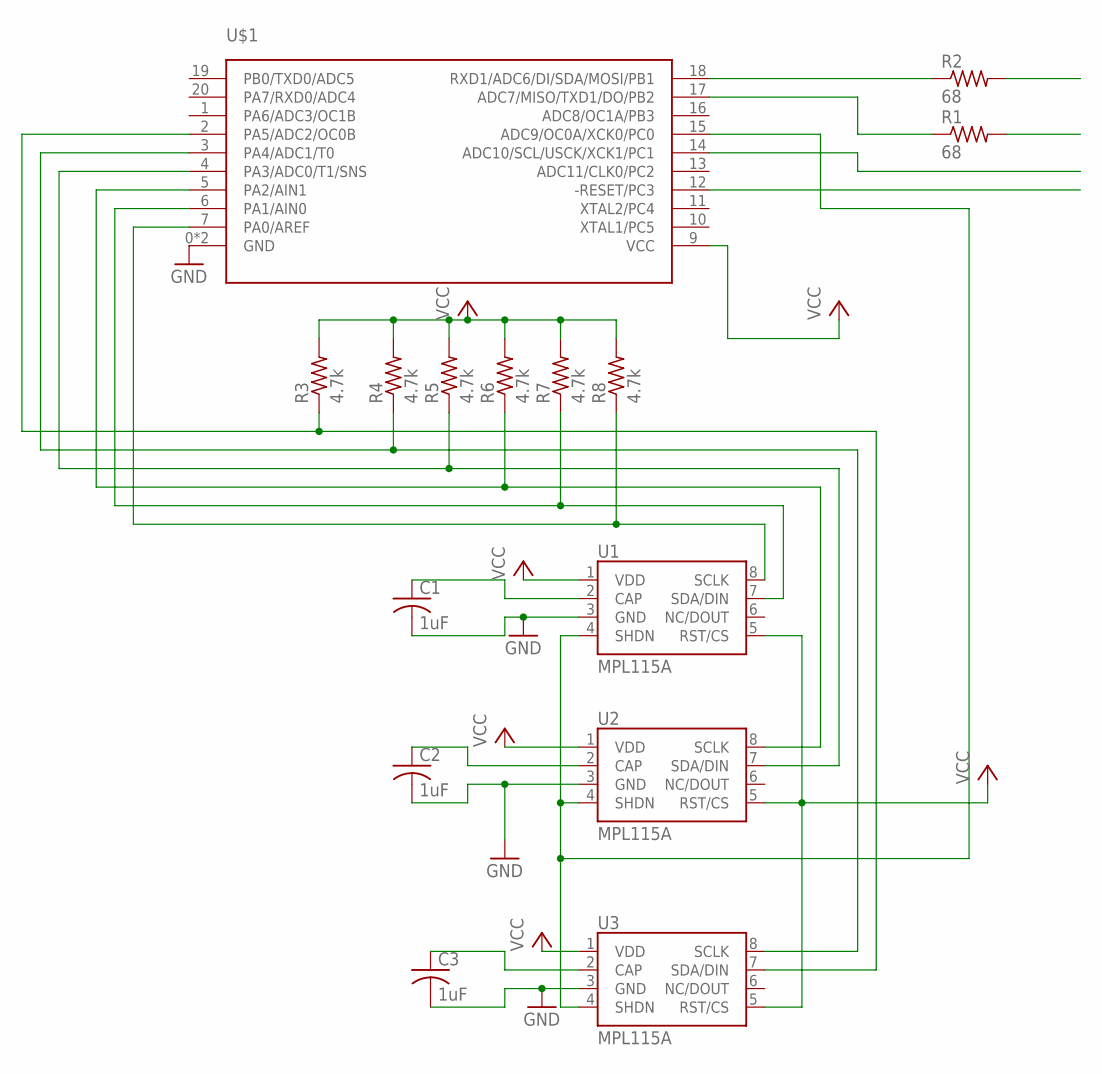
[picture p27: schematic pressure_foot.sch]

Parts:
C1, C2, C3: 1uF; C0603
R1, R2: 68; R0603
R3, R4, R5, R6, R7, R8: 4.7k; R0603
U1, U2, U3: MPL115A; LGA8
U$1: ATTINY1634QFN20; QFN20

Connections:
GND: C1.2, C2.2, C3.2, U1.3 (GND), U2.3 (GND), U3.3 (GND), U$1.0 (GND), U$1.8 (GND)
unnamed: R8.1, U1.8 (SCLK), U$1.7 (PA0/AREF)
unnamed: R2.1, U$1.18 (RXD1/ADC6/DI/SDA/MOSI/PB1)
unnamed: R1.1, U$1.17 (ADC7/MISO/TXD1/DO/PB2)
unnamed: C1.1, U1.2 (CAP)
unnamed: C3.1, U3.2 (CAP)
unnamed: R6.1, U2.8 (SCLK), U$1.5 (PA2/AIN1)
unnamed: R5.1, U2.7 (SDA/DIN), U$1.4 (PA3/ADC0/T1/SNS)
unnamed: U1.4 (SHDN), U2.4 (SHDN), U3.4 (SHDN), U$1.15 (ADC9/OC0A/XCK0/PC0)
unnamed: C2.1, U2.2 (CAP)
unnamed: R7.1, U1.7 (SDA/DIN), U$1.6 (PA1/AIN0)
unnamed: R4.1, U3.8 (SCLK), U$1.3 (PA4/ADC1/T0)
unnamed: R3.1, U3.7 (SDA/DIN), U$1.2 (PA5/ADC2/OC0B)
VCC: R3.2, R4.2, R5.2, R6.2, R7.2, R8.2, U1.1 (VDD), U1.5 (RST/CS), U2.1 (VDD), U2.5 (RST/CS), U3.1 (VDD), U3.5 (RST/CS), U$1.9 (VCC)

Board: 2 copper layers, 15 parts (3 on the bottom side), 14 nets, no tracks yet.

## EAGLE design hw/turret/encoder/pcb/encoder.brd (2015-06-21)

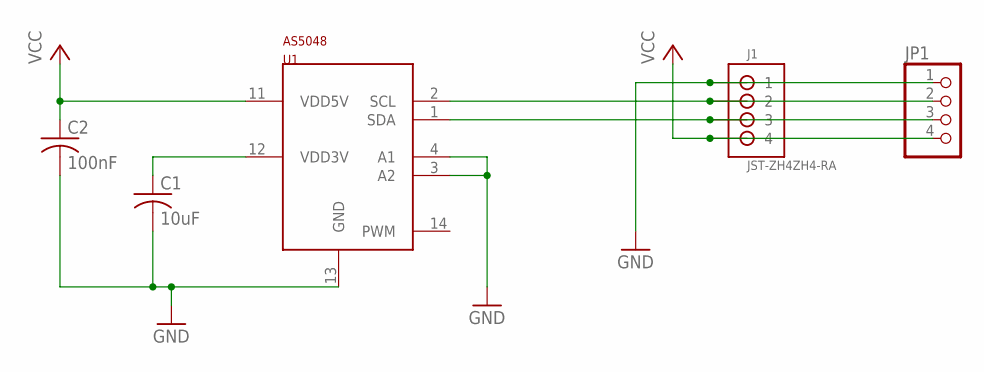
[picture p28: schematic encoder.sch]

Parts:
C1: 10uF; C0603
C2: 100nF; C0603
J1: JST-ZH4ZH4-RA; JST_ZH4_RA
JP1: PINHD-1X4; 1X04
U1: AS5048BTSSOP14; TSSOP14

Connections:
GND: C1.2, C2.2, J1.1, JP1.1, U1.3 (A2), U1.4 (A1), U1.13 (GND)
unnamed: C1.1, U1.12 (VDD3V)
unnamed: J1.2, JP1.2, U1.2 (SCL)
unnamed: J1.3, JP1.3, U1.1 (SDA)
VCC: C2.1, J1.4, JP1.4, U1.11 (VDD5V)

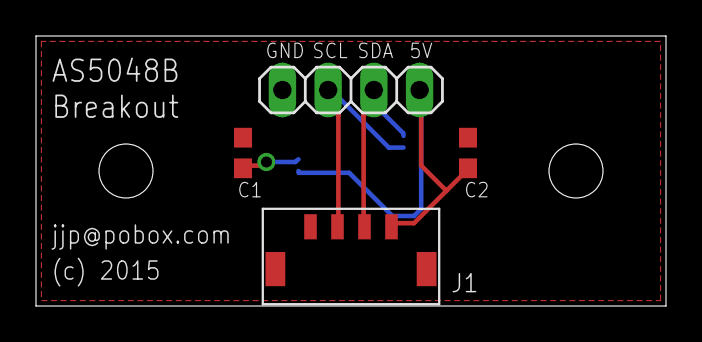
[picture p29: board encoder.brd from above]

Board: 2 copper layers, 35.0 x 15.0 mm, 5 parts (1 on the bottom side), 5 nets.

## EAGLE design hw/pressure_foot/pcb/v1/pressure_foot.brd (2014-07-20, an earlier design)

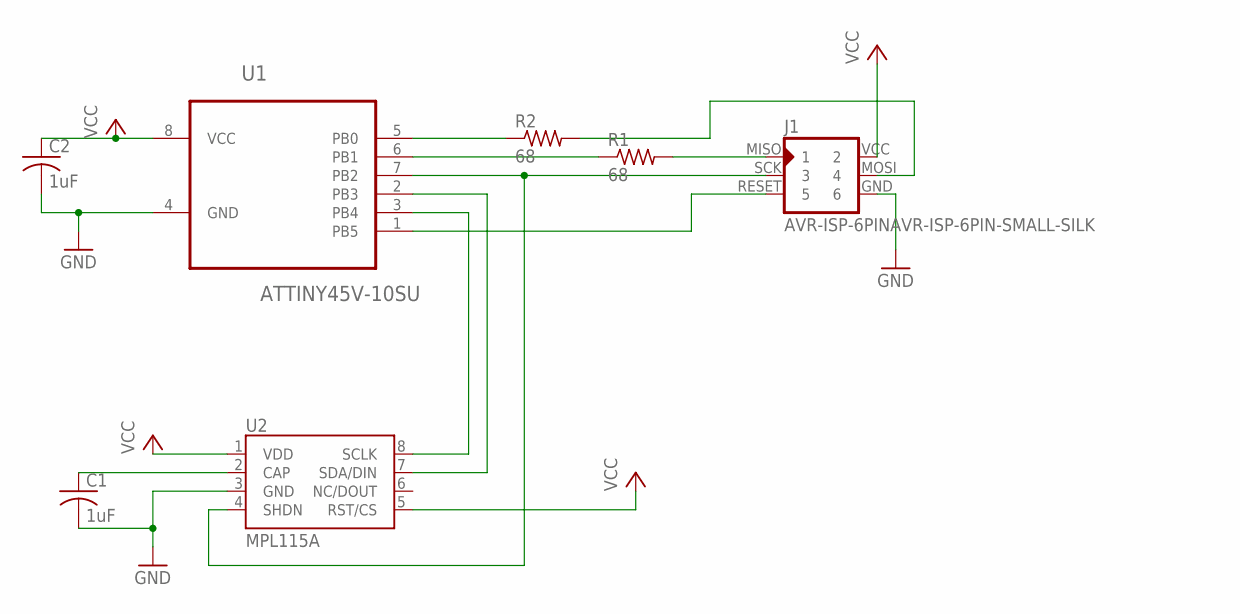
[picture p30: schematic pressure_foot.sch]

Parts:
C1, C2: 1uF; C0603
J1: AVR-ISP-6PINAVR-ISP-6PIN-SMALL-SILK; AVR-ISP-6PIN-SMAILL-SILK
R1, R2: 68; R0603
U1: ATTINY45V-10SU; SOIC127P798X216-8N
U2: MPL115A; LGA8

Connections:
GND: C1.2, C2.2, J1.GND (6), U1.4 (GND), U2.3 (GND)
unnamed: J1.RESET (5), U1.1 (PB5)
unnamed: J1.MISO (1), R1.2
unnamed: R2.1, U1.5 (PB0)
unnamed: R1.1, U1.6 (PB1)
unnamed: J1.MOSI (4), R2.2
unnamed: C1.1, U2.2 (CAP)
unnamed: U1.3 (PB4), U2.8 (SCLK)
unnamed: U1.2 (PB3), U2.7 (SDA/DIN)
unnamed: J1.SCK (3), U1.7 (PB2), U2.4 (SHDN)
VCC: C2.1, J1.VCC (2), U1.8 (VCC), U2.1 (VDD), U2.5 (RST/CS)

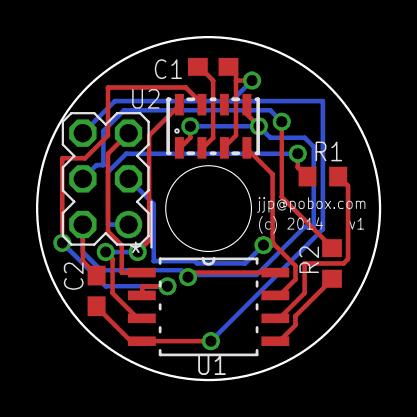
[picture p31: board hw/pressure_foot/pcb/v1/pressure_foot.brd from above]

Board: 2 copper layers, 19.0 x 19.0 mm, 7 parts (0 on the bottom side), 11 nets.

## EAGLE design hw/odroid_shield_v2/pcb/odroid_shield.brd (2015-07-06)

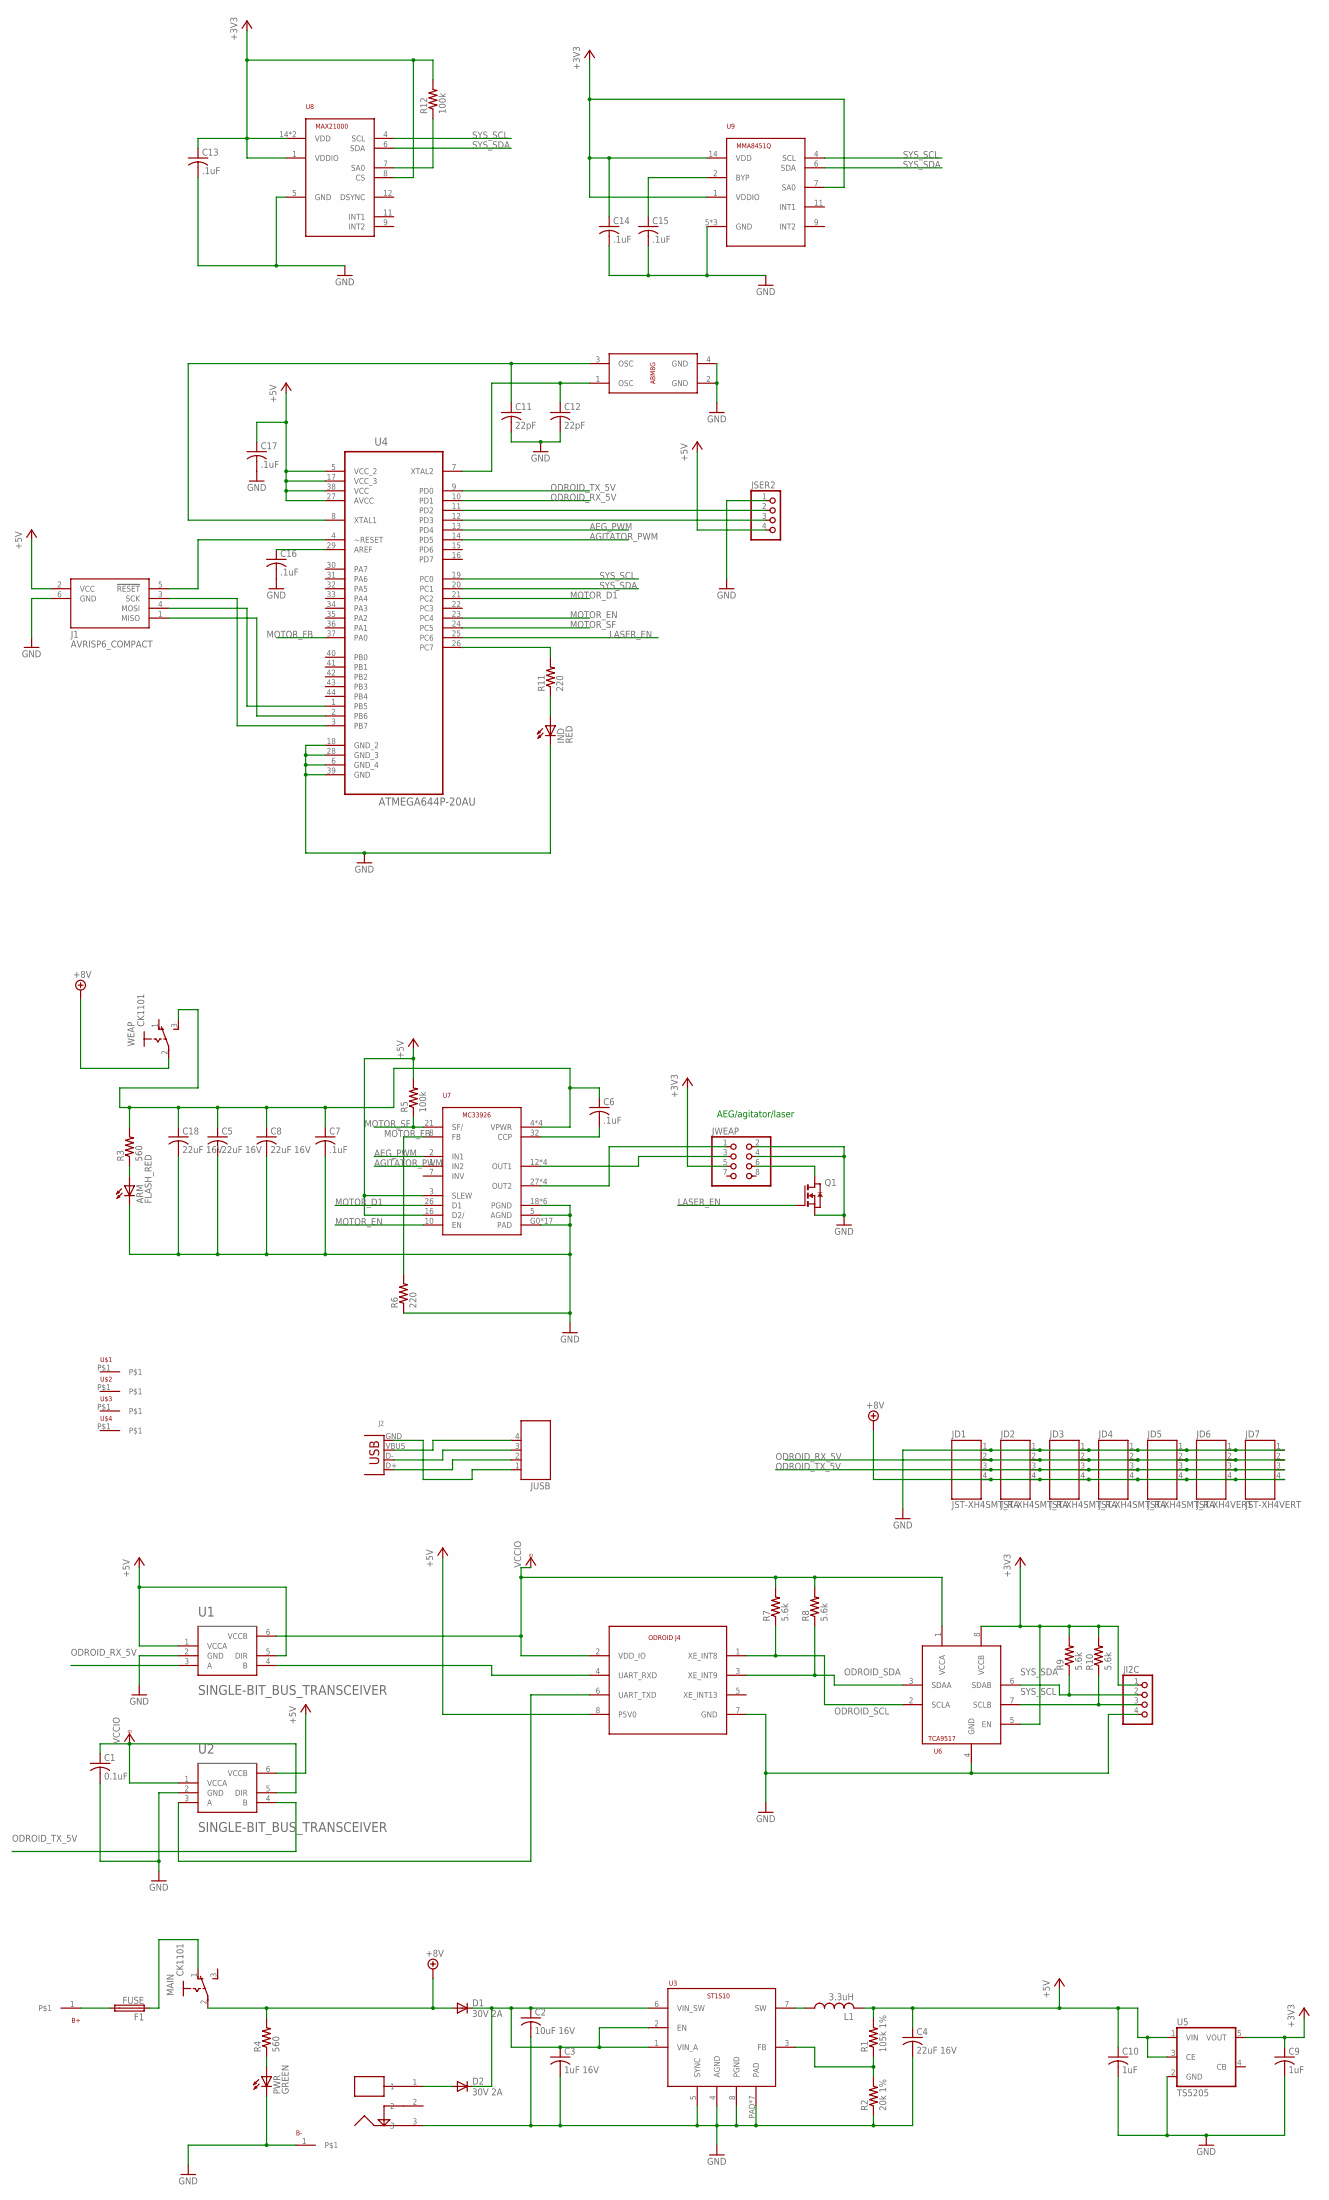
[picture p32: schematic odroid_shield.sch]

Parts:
ARM: FLASH_RED; LED5MM
B+: BAT_TERM
B-: BAT_TERM
C1: 0.1uF; C0603
C2: 10uF 16V; C1206
C3: 1uF 16V; C0603
C4, C5, C8, C18: 22uF 16V; C1210
C6, C7, C13, C14, C15, C16, C17: .1uF; C0603
C9, C10: 1uF; C0603
C11, C12: 22pF; C0603
D1, D2: 30V 2A; CMS06
F1: FUSE; KEYSTONE_HORIZ_FUSE_CLIP
IND: RED; CHIPLED_0805
J1: AVRISP6_COMPACT; CON6P2R
J2: USB2MM; 1X04/2MM
J4: ODROID_J4; 2X04/2MM
JD1, JD2, JD3, JD4, JD5: JST-XH4SMT_RA; JST_XH_SMT_RA_4
JD6, JD7: JST-XH4VERT; JST_XH_VERT_4
JI2C: PINHD-1X4; 1X04
JSER2: PINHD-1X4; 1X04
JUSB: JST-PH4
JWEAP: PINHD-2X4; 2X04
L1: 3.3uH; WURTH_74404042033
MAIN: CK1101; CK1101C
PWR: GREEN; CHIPLED_0805
Q1: NMOSSOT23; SOT-23
R1: 105k 1%; R0603
R2: 20k 1%; R0603
R3, R4: 560; R0603
R5, R12: 100k; R0603
R6, R11: 220; R0603
R7, R8, R9, R10: 5.6k; R0603
SHORE: PJ-034ASMT; CUI_PJ_015AH_SMT
U1, U2: SINGLE-BIT_BUS_TRANSCEIVER; SOT23-6
U3: ST1S10; POWER_SO8
U4: ATMEGA644P-20AU; QFP80P1200X1200X120-44N
U5: TS5205; SOT25
U6: TCA9517MSOP8; MSOP8
U7: MC33926; PQFN32
U8: MAX21000; LGA16
U9: MMA8451Q; QFN16
U10: ABM8G
U$1, U$2, U$3, U$4: M3_HEX_MOUNT
WEAP: CK1101; CK1101C

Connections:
+3V3: C9.1, C13.1, C14.1, JI2C.1, JWEAP.5, R9.2, R10.2, R12.2, U5.5 (VOUT), U6.5 (EN), U6.8 (VCCB), U8.1 (VDDIO), U8.8 (CS), U8.14 (VDD), U8.15 (VDD), U9.1 (VDDIO), U9.7 (SA0), U9.14 (VDD)
+5V: C4.1, C10.1, C17.1, J1.2 (VCC), J4.8 (P5V0), JSER2.4, L1.2, R1.2, R5.2, U1.1 (VCCA), U1.5 (DIR), U2.6 (VCCB), U4.5 (VCC_2), U4.17 (VCC_3), U4.27 (AVCC), U4.38 (VCC), U5.1 (VIN), U5.3 (CE), U7.3 (SLEW), U7.16 (D2/)
+8V: D1.1 (A), JD1.4, JD2.4, JD3.4, JD4.4, JD5.4, JD6.4, JD7.4, MAIN.2, R4.2, WEAP.2
AEG_PWM: U4.13 (PD4), U7.2 (IN1)
AGITATOR_PWM: U4.14 (PD5), U7.1 (IN2)
GND: ARM.K (C), B-.1, C1.2, C2.2, C3.2, C4.2, C5.2, C7.2, C8.2, C9.2, C10.2, C11.2, C12.2, C13.2, C14.2, C15.2, C16.2, C17.2, C18.2, IND.C, J1.6 (GND), J4.7 (GND), JD1.1, JD2.1, JD3.1, JD4.1, JD5.1, JD6.1, JD7.1, JI2C.4, JSER2.1, JWEAP.2, JWEAP.4, PWR.C, Q1.2 (S), R2.1, R6.1, SHORE.3, U1.2 (GND), U2.2 (GND), U3.4 (AGND), U3.5 (SYNC), U3.8 (PGND), U3.PAD, U3.PAD1 (PAD), U3.PAD2 (PAD), U3.PAD3 (PAD), U3.PAD4 (PAD), U3.PAD5 (PAD), U3.PAD6 (PAD), U4.6 (GND_4), U4.18 (GND_2), U4.28 (GND_3), U4.39 (GND), U5.2 (GND), U6.4 (GND), U7.5 (AGND), U7.18 (PGND), U7.19 (PGND), U7.20 (PGND), U7.22 (PGND), U7.23 (PGND), U7.24 (PGND), U7.G0 (PAD), U7.G1 (PAD), U7.G2 (PAD), U7.G3 (PAD), U7.G4 (PAD), U7.G5 (PAD), U7.G6 (PAD), U7.G7 (PAD), U7.G8 (PAD), U7.G9 (PAD), U7.G10 (PAD), U7.G11 (PAD), U7.G12 (PAD), U7.G13 (PAD), U7.G14 (PAD), U7.G15 (PAD), U7.G16 (PAD), U8.5 (GND), U9.5 (GND), U9.10 (GND), U9.12 (GND), U10.2 (GND), U10.4 (GND)
LASER_EN: Q1.3 (G), U4.25 (PC6)
MOTOR_D1: U4.21 (PC2), U7.26 (D1)
MOTOR_EN: U4.23 (PC4), U7.10 (EN)
MOTOR_FB: R6.2, U4.37 (PA0), U7.8 (FB)
MOTOR_SF: R5.1, U4.24 (PC5), U7.21 (SF/)
unnamed: J2.VBUS, JUSB.4
unnamed: J4.4 (UART_RXD), U1.4 (B)
unnamed: J2.D-, JUSB.3
unnamed: J4.6 (UART_TXD), U2.3 (A)
unnamed: J2.D+, JUSB.2
unnamed: J2.GND, JUSB.1
unnamed: B+.1, F1.3 (2), F1.4 (2)
unnamed: F1.1, F1.2 (1), MAIN.1 (O)
unnamed: D2.1 (A), SHORE.1
unnamed: L1.1, U3.7 (SW)
unnamed: C2.1, C3.1, D1.2 (C), D2.2 (C), U3.1 (VIN_A), U3.2 (EN), U3.6 (VIN_SW)
unnamed: JWEAP.1, U7.27 (OUT2), U7.28 (OUT2), U7.29 (OUT2), U7.30 (OUT2)
unnamed: R1.1, R2.2, U3.3 (FB)
unnamed: JWEAP.3, U7.12 (OUT1), U7.13 (OUT1), U7.14 (OUT1), U7.15 (OUT1)
unnamed: C5.1, C6.1, C7.1, C8.1, C18.1, R3.2, U7.4 (VPWR), U7.6 (VPWR), U7.11 (VPWR), U7.31 (VPWR), WEAP.3 (S)
unnamed: C6.2, U7.32 (CCP)
unnamed: R11.2, U4.26 (PC7)
unnamed: R12.1, U8.7 (SA0)
unnamed: JWEAP.6, Q1.1 (D)
unnamed: ARM.A, R3.1
unnamed: J1.5 (!RESET), U4.4 (~RESET)
unnamed: PWR.A, R4.1
unnamed: J1.3 (SCK), U4.3 (PB7)
unnamed: J1.4 (MOSI), U4.1 (PB5)
unnamed: J1.1 (MISO), U4.2 (PB6)
unnamed: JSER2.3, U4.12 (PD3)
unnamed: JSER2.2, U4.11 (PD2)
unnamed: IND.A, R11.1
unnamed: C16.1, U4.29 (AREF)
unnamed: C12.1, U4.7 (XTAL2), U10.1 (OSC)
unnamed: C11.1, U4.8 (XTAL1), U10.3 (OSC)
unnamed: C15.1, U9.2 (BYP)
ODROID_RX_5V: JD1.2, JD2.2, JD3.2, JD4.2, JD5.2, JD6.2, JD7.2, U1.3 (A), U4.10 (PD1)
ODROID_SCL: J4.1 (XE_INT8), R7.1, U6.2 (SCLA)
ODROID_SDA: J4.3 (XE_INT9), R8.1, U6.3 (SDAA)
ODROID_TX_5V: JD1.3, JD2.3, JD3.3, JD4.3, JD5.3, JD6.3, JD7.3, U2.4 (B), U4.9 (PD0)
SYS_SCL: JI2C.3, R10.1, U4.19 (PC0), U6.7 (SCLB), U8.4 (SCL), U9.4 (SCL)
SYS_SDA: JI2C.2, R9.1, U4.20 (PC1), U6.6 (SDAB), U8.6 (SDA), U9.6 (SDA)
VCCIO: C1.1, J4.2 (VDD_IO), R7.2, R8.2, U1.6 (VCCB), U2.1 (VCCA), U2.5 (DIR), U6.1 (VCCA)

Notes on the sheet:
AEG/agitator/laser

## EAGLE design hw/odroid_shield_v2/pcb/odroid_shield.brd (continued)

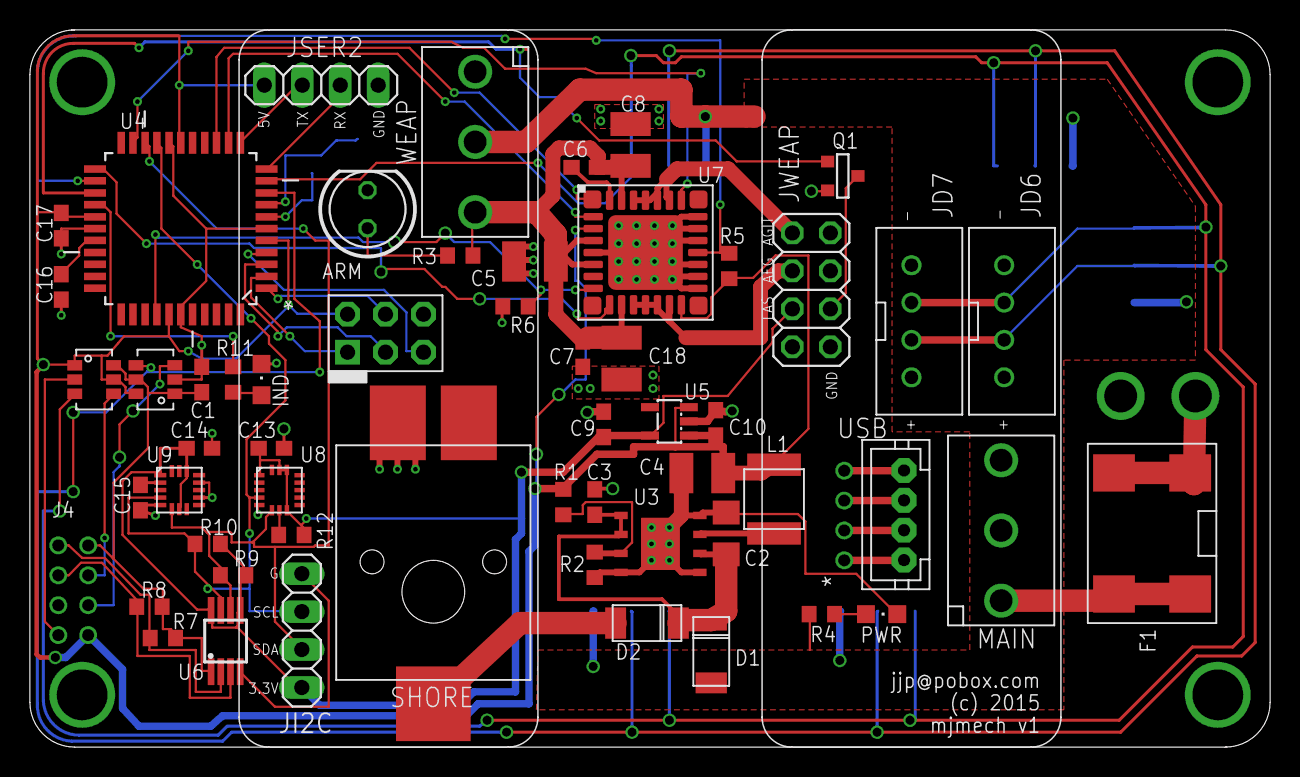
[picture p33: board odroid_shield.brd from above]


Board: 2 copper layers, 83.0 x 48.0 mm, 71 parts (11 on the bottom side), 50 nets.

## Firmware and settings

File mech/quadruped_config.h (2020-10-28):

// Copyright 2019-2020 Josh Pieper, jjp@pobox.com.
//
// Licensed under the Apache License, Version 2.0 (the "License");
// you may not use this file except in compliance with the License.
// You may obtain a copy of the License at
//
//     http://www.apache.org/licenses/LICENSE-2.0
//
// Unless required by applicable law or agreed to in writing, software
// distributed under the License is distributed on an "AS IS" BASIS,
// WITHOUT WARRANTIES OR CONDITIONS OF ANY KIND, either express or implied.
// See the License for the specific language governing permissions and
// limitations under the License.

#pragma once

#include <vector>

#include "mjlib/base/visitor.h"

#include "base/point3d.h"
#include "base/sophus.h"
#include "mech/mammal_ik.h"

namespace mjmech {
namespace mech {

// This represents the JSON used to configure the geometry of the
// robot.
struct QuadrupedConfig {
  double period_s = 0.0025;
  double min_voltage = 16.0;

  struct Joint {
    int id = 0;
    double sign = 1.0;
    double rezero_pos_deg = 0.0;

    template <typename Archive>
    void Serialize(Archive* a) {
      a->Visit(MJ_NVP(id));
      a->Visit(MJ_NVP(sign));
      a->Visit(MJ_NVP(rezero_pos_deg));
    }
  };

  std::vector<Joint> joints;

  // The maximum error is about +-30 deg, so this will at least catch
  // some fraction of failures to position properly at startup.
  double rezero_threshold_deg = 15.0;

  struct Leg {
    int leg = 0;
    Sophus::SE3d pose_BG;
    MammalIk::Config ik;

    template <typename Archive>
    void Serialize(Archive* a) {
      a->Visit(MJ_NVP(leg));
      a->Visit(MJ_NVP(pose_BG));
      a->Visit(MJ_NVP(ik));
    }
  };

  std::vector<Leg> legs;

  struct Bounds {
    double min_z_B = 0.0;
    double max_z_B = 0.3;
    double max_acceleration = 100;

    template <typename Archive>
    void Serialize(Archive* a) {
      a->Visit(MJ_NVP(min_z_B));
      a->Visit(MJ_NVP(max_z_B));
      a->Visit(MJ_NVP(max_acceleration));
    }
  };

  Bounds bounds;

  double mass_kg = 10.0;
  double leg_mass_kg = 0.5;
  base::Point3D center_of_mass_B;

  struct StandUp {
    // This pose is referenced to the leg in the front right and the
    // x/y positions should all be positive.  All other positions will
    // be symmetric about the x/y axes.
    base::Point3D pose_R = {0.151, 0.219, 0.049};
    double velocity_dps = 60.0;
    double velocity = 0.150;
    double shoulder_clearance_deg = 52.0;
    double max_preposition_torque_Nm = 3.0;
    double preposition_kp_scale = 5.0;
    double timeout_s = 10.0;
    double tolerance_deg = 1.0;
    double tolerance_m = 0.001;
    double acceleration = 2.000;

    template <typename Archive>
    void Serialize(Archive* a) {
      a->Visit(MJ_NVP(pose_R));
      a->Visit(MJ_NVP(velocity_dps));
      a->Visit(MJ_NVP(velocity));
      a->Visit(MJ_NVP(shoulder_clearance_deg));
      a->Visit(MJ_NVP(max_preposition_torque_Nm));
      a->Visit(MJ_NVP(preposition_kp_scale));
      a->Visit(MJ_NVP(timeout_s));
      a->Visit(MJ_NVP(tolerance_deg));
      a->Visit(MJ_NVP(tolerance_m));
      a->Visit(MJ_NVP(acceleration));
    }
  };

  StandUp stand_up;

  struct Rest {
    double velocity = 0.100;

    template <typename Archive>
    void Serialize(Archive* a) {
      a->Visit(MJ_NVP(velocity));
    }
  };

  Rest rest;

  double stand_height = 0.210;

  double idle_x = 0.190;
  double idle_y = 0.140;

  base::Point3D default_kp_N_m = {1000.0, 1000.0, 200.0};
  base::Point3D default_kd_N_m_s = {20.0, 20.0, 20.0};

  double rb_filter_constant_Hz = 2.0;
  double lr_acceleration = 2.000;
  double lr_alpha_rad_s2 = 1.0;
  double terrain_filter_s = 0.5;
  double voltage_filter_s = 1.0;

  struct Jump {
    double lower_velocity = 0.100;
    double retract_velocity = 1.000;
    double retract_acceleration = 100.000;
    double land_threshold = 0.015;
    double kp_scale = 10.0;
    double kd_scale = 1.0;
    double land_kp = 1.0;
    double land_kd = 0.1;
    double lower_height = 0.100;
    double upper_height = 0.220;
    double retract_height = 0.190;
    double landing_force_scale = 1.0;
    double land_gain_increase = 100.0;
    double min_acceleration = 0.500;
    double land_velocity = 0.01;

    template <typename Archive>
    void Serialize(Archive* a) {
      a->Visit(MJ_NVP(lower_velocity));
      a->Visit(MJ_NVP(retract_velocity));
      a->Visit(MJ_NVP(retract_acceleration));
      a->Visit(MJ_NVP(land_threshold));
      a->Visit(MJ_NVP(kp_scale));
      a->Visit(MJ_NVP(kd_scale));
      a->Visit(MJ_NVP(land_kp));
      a->Visit(MJ_NVP(land_kd));
      a->Visit(MJ_NVP(lower_height));
      a->Visit(MJ_NVP(upper_height));
      a->Visit(MJ_NVP(retract_height));
      a->Visit(MJ_NVP(landing_force_scale));
      a->Visit(MJ_NVP(land_gain_increase));
      a->Visit(MJ_NVP(min_acceleration));
      a->Visit(MJ_NVP(land_velocity));
    }
  };

  Jump jump;

  struct Walk {
    double lift_height = 0.025;
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

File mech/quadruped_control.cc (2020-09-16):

// Copyright 2019-2020 Josh Pieper, jjp@pobox.com.
//
// Licensed under the Apache License, Version 2.0 (the "License");
// you may not use this file except in compliance with the License.
// You may obtain a copy of the License at
//
//     http://www.apache.org/licenses/LICENSE-2.0
//
// Unless required by applicable law or agreed to in writing, software
// distributed under the License is distributed on an "AS IS" BASIS,
// WITHOUT WARRANTIES OR CONDITIONS OF ANY KIND, either express or implied.
// See the License for the specific language governing permissions and
// limitations under the License.

#include "mech/quadruped_control.h"

#include <fstream>

#include <boost/algorithm/string.hpp>
#include <boost/asio/post.hpp>

#include <fmt/format.h>

#include "mjlib/base/clipp_archive.h"
#include "mjlib/base/json5_read_archive.h"

#include "mjlib/io/now.h"
#include "mjlib/io/repeating_timer.h"

#include "base/common.h"
#include "base/fit_plane.h"
#include "base/interpolate.h"
#include "base/logging.h"
#include "base/sophus.h"
#include "base/telemetry_registry.h"
#include "base/timestamped_log.h"

#include "mech/attitude_data.h"
#include "mech/mammal_ik.h"
#include "mech/moteus.h"
#include "mech/quadruped_config.h"
#include "mech/quadruped_context.h"
#include "mech/quadruped_trot.h"
#include "mech/quadruped_util.h"
#include "mech/swing_trajectory.h"
#include "mech/trajectory.h"

namespace pl = std::placeholders;

namespace mjmech {
namespace mech {

namespace {
constexpr int kNumServos = 12;

using QC = QuadrupedCommand;
using QM = QC::Mode;

template <typename Iter, typename Functor>
auto Average(Iter begin, Iter end, Functor f) -> decltype(f(*begin)) {
  using T = decltype(f(*begin));

  T sum = {};
  double count = {};
  for (Iter it = begin; it != end; ++it) {
    count++;
    sum += f(*it);
  }
  return (1.0 / count) * sum;
}

template <typename Iter, typename Functor>
auto Max(Iter begin, Iter end, Functor f) -> decltype(f(*begin)) {
  using T = decltype(f(*begin));

  MJ_ASSERT(begin != end);

  T current = f(*begin);
  Iter it = begin;
  ++it;
  for (; it != end; ++it) {
    const auto value = f(*it);
    if (value > current) { current = value; }
  }
  return current;
}

template <typename Iter, typename Functor>
auto Min(Iter begin, Iter end, Functor f) -> decltype(f(*begin)) {
  using T = decltype(f(*begin));

  MJ_ASSERT(begin != end);

  T current = f(*begin);
  Iter it = begin;
  ++it;
  for (; it != end; ++it) {
    const auto value = f(*it);
    if (value < current) { current = value; }
  }
  return current;
}

struct ReportedServoConfig {
  boost::posix_time::ptime timestamp;

  struct Servo {
    int id = 0;
    int rezero_state = 0;
    int register_map_version = -1;
    std::array<uint8_t, 12> serial_number = {};

    template <typename Archive>
    void Serialize(Archive* a) {
      a->Visit(MJ_NVP(id));
      a->Visit(MJ_NVP(rezero_state));
      a->Visit(MJ_NVP(register_map_version));
      a->Visit(MJ_NVP(serial_number));
    }
  };

  std::vector<Servo> servos;

  template <typename Archive>
  void Serialize(Archive* a) {
    a->Visit(MJ_NVP(timestamp));
    a->Visit(MJ_NVP(servos));
  }
};

using Config = QuadrupedConfig;

struct CommandLog {
  boost::posix_time::ptime timestamp;

  const QC* command = &ignored_command;

  template <typename Archive>
  void Serialize(Archive* a) {
    a->Visit(MJ_NVP(timestamp));
    const_cast<QC*>(command)->Serialize(a);
  }

  static QC ignored_command;
};

QC CommandLog::ignored_command;
}

class QuadrupedControl::Impl {
 public:
  Impl(base::Context& context,
       Pi3hatGetter pi3hat_getter)
      : executor_(context.executor),
        telemetry_log_(context.telemetry_log.get()),
        timer_(executor_),
        pi3hat_getter_(pi3hat_getter) {
    context.telemetry_registry->Register("qc_status", &status_signal_);
    context.telemetry_registry->Register("qc_command", &command_signal_);
    context.telemetry_registry->Register("qc_control", &control_signal_);
    context.telemetry_registry->Register("imu", &imu_signal_);
    context.telemetry_registry->Register("servo_config", &servo_config_signal_);
  }

  void AsyncStart(mjlib::io::ErrorCallback callback) {
    pi3hat_ = pi3hat_getter_();

    BOOST_ASSERT(!!pi3hat_);

    // Load our configuration.
    std::vector<std::string> configs;
    boost::split(configs, parameters_.config, boost::is_any_of(" "));
    for (const auto& config : configs) {
      std::ifstream inf(config);
      mjlib::base::system_error::throw_if(
          !inf.is_open(),
          fmt::format("could not open config file '{}'", parameters_.config));

      mjlib::base::Json5ReadArchive(inf).Accept(&config_);
    }

    if (config_.legs.size() != 4 ||
        config_.joints.size() != kNumServos) {
      mjlib::base::Fail(
          fmt::format(
              "Incorrect number of legs/joints configured: {}/{} != 4/12",
              config_.legs.size(), config_.joints.size()));
    }

    context_.emplace(config_, &current_command_, &status_.state);

    PopulateStatusRequest();

    period_s_ = config_.period_s;
    timer_.start(mjlib::base::ConvertSecondsToDuration(period_s_),
                 std::bind(&Impl::HandleTimer, this, pl::_1));

    boost::asio::post(
        executor_,
        std::bind(std::move(callback), mjlib::base::error_code()));
  }

  void Command(const QC& command) {
    const auto now = Now();
    const bool higher_priority = command.priority >= current_command_.priority;
    const bool stale =
        !current_command_timestamp_.is_not_a_date_time() &&
        (mjlib::base::ConvertDurationToSeconds(
            now - current_command_timestamp_) > parameters_.command_timeout_s);
    if (!higher_priority && !stale) {
      return;
    }

    CommandLog command_log;
    command_log.timestamp = now;
    command_log.command = &command;

    current_command_ = command;
    current_command_timestamp_ = now;

    // Update our logging status.
    if (command.log != QuadrupedCommand::Log::kUnset) {
      if (command.log == QuadrupedCommand::Log::kEnable &&
          !telemetry_log_->IsOpen()) {
        base::OpenMaybeTimestampedLog(
            telemetry_log_,
            parameters_.log_filename_base,
            base::kTimestamped);
      } else if (command.log == QuadrupedCommand::Log::kDisable &&
                 telemetry_log_->IsOpen()) {
        telemetry_log_->Close();
      }
    }

    command_signal_(&command_log);
  }

  void PopulateStatusRequest() {
    status_request_ = {};
    for (const auto& joint : config_.joints) {
      status_request_.push_back({});
      auto& current = status_request_.back();
      current.id = joint.id;

      // Read mode, position, velocity, and torque.
      current.request.ReadMultiple(moteus::Register::kMode, 4, 1);
      current.request.ReadMultiple(moteus::Register::kVoltage, 3, 0);

      if (parameters_.servo_debug) {
        current.request.ReadMultiple(moteus::Register::kPositionKp, 5, 1);
      }
    }
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

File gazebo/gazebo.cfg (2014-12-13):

[servo]
type = 1
port = /dev/ttyUSB0
count = 14
model = mj_mech

[servo.poses]
idle = 0=0.00,1=0.00,2=90.00,3=0.00,4=0.00,5=90.00,6=0.00,7=0.00,8=90.00,9=0.00,10=0.00,11=90.00,12=0.00,13=0.00
min = 0=-45.00,1=-90.00,2=-90.00,3=-100.00,4=-90.00,5=-90.00,6=-45.00,7=-90.00,8=-90.00,9=-100.00,10=-90.00,11=-90.00,12=-27.00,13=-6.00
max = 0=100.00,1=100.00,2=110.00,3=45.00,4=100.00,5=110.00,6=100.00,7=100.00,8=110.00,9=45.00,10=100.00,11=110.00,12=6.00,13=-6.00

[servo.names]
0 = coxa_hinge0
1 = femur_hinge0
2 = tibia_hinge0
3 = coxa_hinge1
4 = femur_hinge1
5 = tibia_hinge1
6 = coxa_hinge2
7 = femur_hinge2
8 = tibia_hinge2
9 = coxa_hinge3
10 = femur_hinge3
11 = tibia_hinge3
12 = pan_aeg_hinge
13 = weapon_assembly_hinge

[ikconfig]
idle_pose = idle
minimum_pose = min
maximum_pose = max
x_offset = 0.0
y_offset = 80.0
z_offset = -90.0
coxa_length = 60.0
femur_length = 60.0
tibia_length = 60.0
coxa_mass = 0.06
femur_mass = 0.06
tibia_mass = 0.06
plane = 1
scale = 180.0
speed_scale = 880
speed_axis = 0

[ikconfig.legs]
leg.0 = True,0,-1,1,-1,2,-1
leg.1 = True,3,-1,4,-1,5,-1
leg.2 = True,6,-1,7,-1,8,-1
leg.3 = True,9,-1,10,-1,11,-1
leg.4 = False,0,1,0,1,0,1
leg.5 = False,0,1,0,1,0,1

[ikconfig.leg.0]
servo_speed_dps = 360.0
tibia_ident = 2
femur_ident = 1
tibia_length_mm = 60.0
coxa_mass_kg = 0.06
femur_mass_kg = 0.06
femur_idle_deg = 0.0
coxa_min_deg = -45.0
coxa_idle_deg = 0.0
femur_sign = -1
coxa_ident = 0
tibia_mass_kg = 0.06
coxa_sign = -1
femur_min_deg = -90.0
tibia_min_deg = -90.0
tibia_sign = -1
femur_length_mm = 60.0
coxa_max_deg = 100.0
femur_max_deg = 100.0
tibia_max_deg = 110.0
coxa_length_mm = 60.0
tibia_idle_deg = 90.0

[ikconfig.leg.1]
servo_speed_dps = 360.0
tibia_ident = 5
femur_ident = 4
tibia_length_mm = 60.0
coxa_mass_kg = 0.06
femur_mass_kg = 0.06
femur_idle_deg = 0.0
coxa_min_deg = -100.0
coxa_idle_deg = 0.0
femur_sign = -1
coxa_ident = 3
tibia_mass_kg = 0.06
coxa_sign = -1
femur_min_deg = -90.0
tibia_min_deg = -90.0
tibia_sign = -1
femur_length_mm = 60.0
coxa_max_deg = 45.0
femur_max_deg = 100.0
tibia_max_deg = 110.0
coxa_length_mm = 60.0
tibia_idle_deg = 90.0

[ikconfig.leg.2]
servo_speed_dps = 360.0
tibia_ident = 8
femur_ident = 7
tibia_length_mm = 60.0
coxa_mass_kg = 0.06
femur_mass_kg = 0.06
femur_idle_deg = 0.0
coxa_min_deg = -45.0
coxa_idle_deg = 0.0
femur_sign = -1
coxa_ident = 6
tibia_mass_kg = 0.06
coxa_sign = -1
femur_min_deg = -90.0
tibia_min_deg = -90.0
tibia_sign = -1
femur_length_mm = 60.0
coxa_max_deg = 100.0
femur_max_deg = 100.0
tibia_max_deg = 110.0
coxa_length_mm = 60.0
tibia_idle_deg = 90.0

[ikconfig.leg.3]
servo_speed_dps = 360.0
tibia_ident = 11
femur_ident = 10
tibia_length_mm = 60.0
coxa_mass_kg = 0.06
femur_mass_kg = 0.06
femur_idle_deg = 0.0
coxa_min_deg = -100.0
coxa_idle_deg = 0.0
femur_sign = -1
coxa_ident = 9
tibia_mass_kg = 0.06
coxa_sign = -1
femur_min_deg = -90.0
tibia_min_deg = -90.0
tibia_sign = -1
femur_length_mm = 60.0
coxa_max_deg = 45.0
femur_max_deg = 100.0
tibia_max_deg = 110.0
coxa_length_mm = 60.0
tibia_idle_deg = 90.0

[gaitconfig]
max_cycle_time_s = 0.8
lift_height_mm = 20.0
lift_percent = 25.0
swing_percent = 60.0
position_margin_percent = 90.0
body_z_offset_mm = 80.0
servo_speed_margin_percent = 70.0
static_center_factor = 3.0
static_stable_factor = 8.0
static_margin_mm = 25.0
statically_stable = False
leg_order = (0,2),(1,3)
accurate_cog = False
geometry_scale_mm = 200.0
command_x_mm_s = 0.0
command_y_mm_s = 50.0
command_rot_deg_s = 0.0
command_body_x_mm = 0.0
command_body_y_mm = 0.0
command_body_z_mm = 0.0
command_body_pitch_deg = 0.0
command_body_roll_deg = 0.0
command_body_yaw_deg = 0.0
geometry_frame = Body
geometry_projection = X/Y
command_x_axis = Translation X
command_y_axis = Translation Y
command_axis_scale_0 = 250.0
command_axis_scale_1 = 250.0
command_axis_scale_2 = 50.0
command_axis_scale_3 = 100.0
command_axis_scale_4 = 100.0
command_axis_scale_5 = 100.0
command_axis_scale_6 = 45.0
command_axis_scale_7 = 45.0
command_axis_scale_8 = 45.0

[gaitconfig.legs]
leg.0 = 90.00,90.00,0.00,100.00,0.00,0.00
leg.1 = 90.00,-90.00,0.00,100.00,0.00,0.00
leg.2 = -90.00,-90.00,0.00,100.00,0.00,0.00
leg.3 = -90.00,90.00,0.00,100.00,0.00,0.00
body_cog_x_mm = 0.0
body_cog_y_mm = 3.5
body_cog_z_mm = 0.0

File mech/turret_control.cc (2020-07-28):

// Copyright 2020 Josh Pieper, jjp@pobox.com.
//
// Licensed under the Apache License, Version 2.0 (the "License");
// you may not use this file except in compliance with the License.
// You may obtain a copy of the License at
//
//     http://www.apache.org/licenses/LICENSE-2.0
//
// Unless required by applicable law or agreed to in writing, software
// distributed under the License is distributed on an "AS IS" BASIS,
// WITHOUT WARRANTIES OR CONDITIONS OF ANY KIND, either express or implied.
// See the License for the specific language governing permissions and
// limitations under the License.

#include "mech/turret_control.h"

#include <boost/asio/post.hpp>

#include "mjlib/base/clipp_archive.h"
#include "mjlib/base/limit.h"
#include "mjlib/io/repeating_timer.h"

#include "base/logging.h"
#include "base/telemetry_registry.h"

#include "mech/moteus.h"

namespace pl = std::placeholders;

namespace mjmech {
namespace mech {

namespace {
constexpr int kWeaponDivider = 10;  // 40Hz weapon updates

enum WeaponRegister {
  kFirePwm = 0x010,
  kFireTime = 0x011,
  kLoaderPwm = 0x012,
  kLoaderTime = 0x013,
  kLaser = 0x014,
  kShotCount = 0x015,
  kArmed = 0x016,
};

struct CommandLog {
  boost::posix_time::ptime timestamp;

  const TurretControl::CommandData* command = &ignored_command;

  template <typename Archive>
  void Serialize(Archive* a) {
    a->Visit(MJ_NVP(timestamp));
    const_cast<TurretControl::CommandData*>(command)->Serialize(a);
  }

  static inline TurretControl::CommandData ignored_command;
};

struct ControlLog {
  boost::posix_time::ptime timestamp;

  TurretControl::ControlData control;

  template <typename Archive>
  void Serialize(Archive* a) {
    a->Visit(MJ_NVP(timestamp));
    a->Visit(MJ_NVP(control));
  }
};

struct ImageLog {
  boost::posix_time::ptime timestamp;
  std::vector<Eigen::Vector2d> targets;

  template <typename Archive>
  void Serialize(Archive* a) {
    a->Visit(MJ_NVP(timestamp));
    a->Visit(MJ_NVP(targets));
  }
};
}

class TurretControl::Impl {
 public:
  Impl(base::Context& context,
       ClientGetter client_getter,
       ImuGetter imu_getter)
      : executor_(context.executor),
        client_getter_(client_getter),
        imu_getter_(imu_getter) {
    context.telemetry_registry->Register("imu", &imu_signal_);
    context.telemetry_registry->Register("turret", &turret_signal_);
    context.telemetry_registry->Register("command", &command_signal_);
    context.telemetry_registry->Register("control", &control_signal_);
    context.telemetry_registry->Register("image", &image_signal_);
    context.telemetry_registry->Register("weapon", &weapon_signal_);
  }

  void AsyncStart(mjlib::io::ErrorCallback callback) {
    camera_ = std::make_unique<CameraDriver>(parameters_.camera);
    camera_->image_signal()->connect(
        std::bind(&Impl::HandleImage_THREAD, this, pl::_1));
    client_ = client_getter_();
    imu_client_ = imu_getter_();

    PopulateStatusRequest();

    timer_.start(mjlib::base::ConvertSecondsToDuration(parameters_.period_s),
                 std::bind(&Impl::HandleTimer, this, pl::_1));

    boost::asio::post(
        executor_,
        std::bind(std::move(callback), mjlib::base::error_code()));
  }

  void Command(const CommandData& data) {
    const auto now = Now();

    const bool higher_priority = data.priority >= current_command_.priority;
    const bool stale =
        !current_command_timestamp_.is_not_a_date_time() &&
        (mjlib::base::ConvertDurationToSeconds(
            now - current_command_timestamp_) > parameters_.command_timeout_s);

    if (!higher_priority && !stale) {
      return;
    }

    current_command_ = data;
    current_command_timestamp_ = now;

    CommandLog command_log;
    command_log.timestamp = Now();
    command_log.command = &current_command_;
    command_signal_(&command_log);
  }

  // private

  void HandleImage_THREAD(const cv::Mat& image) {
    // WE ARE IN A BG THREAD.
    if (!target_tracker_) {
      target_tracker_ = std::make_unique<TargetTracker>(parameters_.tracker);
    }
    const auto result = target_tracker_->Track(image);

    // Bounce these results back to the main thread.
    boost::asio::post(
        executor_,
        std::bind(&Impl::HandleImage, this, result));
  }

  void HandleImage(TargetTracker::Result result) {
    image_data_.timestamp = Now();
    image_data_.targets = result.targets;
    image_signal_(&image_data_);
  }

  void PopulateStatusRequest() {
    status_request_ = {};
    for (int id : { 1, 2}) {
      status_request_.push_back({});
      auto& current = status_request_.back();
      current.id = id;
      current.request.ReadMultiple(moteus::Register::kMode, 4, 3);
      current.request.ReadMultiple(moteus::Register::kVoltage, 3, 1);
    }

    {
      status_weapon_request_ = status_request_;
      status_weapon_request_.push_back({});
      auto& current = status_weapon_request_.back();
      current.id = 7;
      current.request.ReadMultiple(WeaponRegister::kFirePwm, 7, 1);
    }
  }

  void HandleTimer(const mjlib::base::error_code& ec) {
    if (ec == boost::asio::error::operation_aborted) { return; }
    mjlib::base::FailIf(ec);

    if (!client_) { return; }
    if (outstanding_) { return; }

    timing_ = ControlTiming(executor_, timing_.cycle_start());

    outstanding_ = true;

    status_outstanding_ = 2;
    status_count_ = (status_count_ + 1) % kWeaponDivider;
    status_reply_.clear();

    const auto* this_request =
        (status_count_ == 0) ? &status_weapon_request_ : &status_request_;

    client_->AsyncTransmit(
        this_request, &status_reply_,
        std::bind(&Impl::HandleStatus, this, pl::_1));

    imu_client_->ReadImu(
        &imu_data_, std::bind(&Impl::HandleStatus, this, pl::_1));
  }

  void HandleStatus(const mjlib::base::error_code& ec) {
    mjlib::base::FailIf(ec);

    status_outstanding_--;
    if (status_outstanding_ > 0) { return; }

    imu_signal_(&imu_data_);

    UpdateStatus();

    if (status_count_ == 0) {
      weapon_signal_(&weapon_);
    }

    timing_.finish_status();

    RunControl();
    timing_.finish_control();
  }

  void UpdateServo(const mjlib::multiplex::AsioClient::IdRegisterValue& reply,
                   Status::GimbalServo* servo) {
    servo->id = reply.id;
    const double sign = servo_sign_.at(reply.id);
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

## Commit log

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2015-12-02 gimbal: Try to do a better job of reporting I2C errors, in an effort to diagnose why the controller gets "stuck" semi-often.
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2015-12-02 gimbal: Switch to use a main loop that looks more like what the final one will look like. In the process, fix a few bugs in how things were being linked together, mostly around forgetting to use gsl: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
2015-12-03 gimbal: For now, assert if we ever try to malloc. It would be better to have a link or compile time error, but at least this will be obvious.
    [main.c]
2015-12-03 gimbal: Stm32RawI2C: Draft of class which does I2C using the raw registers rather than using HAL. This also doesn't use interrupts, but instead polls.
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2015-12-04 gimbal: Work on BMI160 driver. Kind works a little bit. At least the scaling is off (or possibly the configuration is off) on the accelerometers. There may be other problems too.
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2015-12-05 gimbal: For now, put debug on the UART, since USB needs fixing.
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2015-12-05 BMI160 breakout: Add a solder jumper to select I2C address. Add silk to denote orientation.
    [bmi160_breakout.brd, bmi160_breakout.sch]
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2015-12-05 bmi160 breakout: Tweak location of V label to have same alignment as others.
    [bmi160_breakout.brd]
2015-12-05 bmi160 breakout: Update primary connector to 0.1" header, as it barely makes the board bigger but makes it a lot more convenient.
    [bmi160_breakout.brd, bmi160_breakout.sch]
2015-12-05 gimbal: Switch to a raw I2C library, rather than the ST HAL one. The HAL library was not ideal, as it has a lot of busy loop polling with poor error messages. It also produces various errors frequent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
2015-12-09 gimbal: pcb: Fix the STM32 footprint. * ripup all autorouted things, (and actually trace with that size) * change all manually routed vias to have a slightly unique size * move stuff around so at lea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
    [gimbal.brd, gimbal.sch]
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2015-12-10 gimbal: stm32_raw_i2c: Try to do a better job of resetting the I2C peripheral if we start with it in a funny state. This seems to most often happen when using the debugger to reset the whole chip whi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
2015-12-12 gimbal: PCB: Fix an r1 defect where C22/C23 and C24/C25 had their silk screens swapped.
    [gimbal.brd]
2015-12-12 gimbal: Attempt to make I2C more robust. Resolve all the TODOs in Stm32RawI2C by resetting the bus and reporting errors after suitable timeouts. Make the Bmi160Driver, once it reaches operational sta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
2015-12-12 gimbal: Bmi160Driver: Improved error recovery:
    * Manage the timer so that we make our next read attempt based upon
    when the last successful attempt started, not when it finished.
    That means the min_operational_delay fudge doesn't need to take
    into account the length of a read frame.
    * In addition to reporting the last i2c error, report the first one.
    This way, bad error handling is more easily evident, since the
    initial error, if handled poorly, will lead to different errors
    later on.
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2015-12-13 gimbal: Stm32RawI2C: Actually get the bus reset procedure to work, after much time in the debugger figuring out how the I2C peripheral behaves.
    Also, update other error handling logic to do a better job of
    recovering without needing to do a full bus reset.
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2015-12-14 gimbal: MahonyImu: Initialize the integral term from an average at startup, and the attitude from a single sample of the accelerometer. This means that we don't have to make the filter slew to the co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
2015-12-15 gimbal: Switch the serial interface to be in the HerkuleX protocol, and fix a few bugs that surfaced during hero testing.
2015-12-15 gimbal: I2C tweaks: * Explicitly set the I2C speed in cpp_gimbal * Slightly decrease how far in advance we start polling the IMU * Decrease significantly the time in error before we reset the bus, we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
2015-12-16 gimbal: pcb: Move things around enough that autoroute once again completes successfully.
    [gimbal.brd]
2015-12-17 link: wireless link setup scripts - Add 'info-networking.txt' which is a braindump for all network-related info - Convert setup_wifi_link script from sh to py, as it was getting too big - Add the sup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
2015-12-17 gimbal: Snapshot of board rework. This doesn't currently autoroute, but has the motor enable lines connected to something. It also has a lot of pin swaps in an attempt to clean up the routing.
    [gimbal.brd, gimbal.sch]
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2015-12-19 gimbal: Get the board to be close to routable again, and also connect up the BLDC_FAULT2 signal, which I goofed and didn't actually connect.
    [gimbal.brd, gimbal.sch]
2015-12-19 gimbal: Fix enough things to make the AS5048 work in SPI mode.
2015-12-19 gimbal: Board: Update test point names to be meaningful, and fix labels on weapon connector.
    [gimbal.brd, gimbal.sch]
2015-12-19 gimbal: Tweak silk placement for a few parts to make them line up better.
    [gimbal.brd]
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2015-12-27 simulator: Checkpoint of simulator which kind of builds a mammal mech model. The joints aren't likely to be correct, and neither is the overall positioning.
2015-12-27 simulator: Make the model be roughly correctly linked. * The joints move in the correct axis. * The model is upright and above the ground. * You can use the keyboard to move all of the joints.
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2016-01-01 simulator: Make the robot be much closer to physically real: * Limited the maximum speed and force of each servo joint. * Use somewhat correct mass and moment of inertia * Start trying to model the f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
2016-01-14 simulator: Attempt to fill in values for the IMU simulation. It seems likely I have some signs and rotations wrong, but this at least makes it through to the UKF on the mech and does not incredibly s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
2016-01-15 simulator: Get all rates and linear accelerations to be at least the correct sign for my sample experiments.
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2016-01-23 real.cfg: Switch the joint direction so that all joints have the knee pointing away from the body. This seems to work better with a fully weighed down robot.
    [real.cfg]
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2016-01-23 gimbal: Stm32RawI2C: Random whitespace fix.
2016-01-23 gimbal: Updates for the actual board: * Weapon enable is active positive. * TIM3 doesn't need the special timex complement handling, so make a generic pwm class for that purpose.
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2016-01-23 gimbal: GimbalStabilizer: Actually enable the DRV8313 sleep and reset lines, and provide a configuration option to select whether the boost regulator is used.
2016-01-24 gimbal: Switch to using boost's CRC, because the STM hardware accelerated one appears to be broken and I don't feel like debugging it now.
2016-01-24 gimbal: Make the ARM switch properly arm the motor driver. Previously, we were accidentally trying to drive the switch output from the SMT32, which only kind of worked because I hadn't soldered the s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
    Now, also flash one of the LEDs any time we are armed.
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2016-01-25 gimbal: The body z rate has opposite sign from yaw, so fix it up in the places that assumed they were consistent.
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2016-01-26 Update the real config to be something that works better with the current servo configuration.
    [real.cfg]
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2016-01-29 turret: Modify to be stateless and rely on the gimbal board to do rate based operation.
    Also, fix up HerkuleX so that writing values obeys bit_align, and use
    HerkuleXConstants::Register for all the definitions in turret.
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2016-02-01 gimbal: BldcEncoder: Report errors received from the underlying transport.
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2016-02-01 ServoMonitor: Treat synchronization errors the same as timeouts, since the turret already does so too.
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2016-02-01 gimbal: PCB: Fix spacing of switch alignment pins.
    [gimbal.brd, gimbal.sch]
2016-02-02 gimbal: PCB: Fix the pin ordering on the programming connector.
    [gimbal.brd, gimbal.sch]
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2016-02-04 weapon: Update turret plate design: * Remove HerkuleX mounting points * Add gimbal mounting points
    [turret_no_servos.fcstd]
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2016-02-04 lizard chassis: Update the turret adapter plate to have the hole pattern for a gimbal motor.
    [chassis.fcstd]
2016-02-06 gimbal: If we have a rate fault, no longer latch it forever. Instead, just fault the gimbal stabilizer in the normal way, and let a torque off event reset things.
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2016-02-07 gimbal: Put the HerkuleX status values into the correct location in a STAT packet, and fill in the "motor_on" flag with the value of torque_on.
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2016-02-09 lizard chassis: Make turret mount plate have an alternate pattern 1.5mm further towards the back.
    [chassis.fcstd]
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2016-02-10 real.cfg: Update with slightly better config for real robot when loaded on carpet.
    [real.cfg]
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2016-02-10 Provide a new gimbal config with updated constants. Notably, this enables the boost converter, now that derating is supported.
    [gimbal_config.txt]
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2016-02-11 video: show h264 caps which we send over the wire; force the right caps on the appsink. This allows one to use non-h264 cameras over the network, and fixes sender-side video recording.
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2016-02-14 Create a new gimbal bracket that is the minimum width and has all the appropriate mounting holes and spacers.
    [gimbal_board.iges, gimbal_bracket_r2.stl, mammal_chassis.fcstd]
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2016-02-25 configs: Update lizard config to something which will work and tweak all gait update rates to be at 80Hz.
    [lizard.cfg]
2016-02-26 McastVideoLink: Fix a trivial bug that mis-calculated the total remaining bytes necessary for a given frame, resulting in assertions.
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2016-02-26 VideoControllerApp: Attempt to display the minimal telemetry as an OSD overlay, using the gstreamer textoverlay element. The simulator doesn't present useful information for anything we care about cu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
2016-02-29 gimbal: When enabling torque, we were accidentally using the wrapped yaw to initialize the target, which was expecting unwrapped yaw. Also, when enabling torque, just use the current yaw as the desir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
2016-02-29 configs: Add gimbal configuration for the gimbal currently on the lizard robot.
    [lizard_gimbal_config.txt]
2016-03-01 GstMainLoop: Fix thread safety issues that come up when destroying itself immediately after creating it.
2016-03-01 GstMainLoop: SignalReady was expected to be called from the gstreamer thread, and wasn't actually critical to the problems I was solving earlier. Put it back to being called from a gstreamer thread.
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2016-03-06 MechWarfare: Add a flag to Drive mode which temporarily prevents rotating the base to get into position. Make the controller set this flag when one of the shoulder buttons is pressed. This should all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
2016-03-11 MechWarfareCommand: Make the "start" button toggle whether to stop sending messages. This can be used to reset the servos.
2016-03-14 Add a shoulder bracket for the mammal chassis which attaches to both sides of the servo.
    [shoulder_bracket.fcstd, shoulder_bracket.stl]
2016-03-30 mech_warfare_command: Get the correct start button for the logitech joystick and start paused by default.
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2016-08-06 Bent metal bracket for shoulder.
    [shoulder_bracket_plate.fcstd]
2016-08-07 Gravity feed for panel qual fixture.
    [gravity_feed.fcstd, gravity_feed_bottom.stl, gravity_feed_top.stl]
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2016-11-06 Add input reverse protection and fuse.
    [joule_shield.brd, joule_shield.sch]
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2016-11-07 Add part numbers for all the major ICs and schematic for SD card.
    [joule_shield.brd, joule_shield.sch]
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2016-11-30 Replace USB electrolytics with ceramics. Get everything placed but the RTC battery.
    [joule_shield.brd, joule_shield.sch]
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2016-12-01 joule shield: Switch to a smaller RTC battery and get everything on the board.
    [joule_shield.brd, joule_shield.sch]
2016-12-01 joule_shield: Swap SD level converter for one with a 0.5mm BGA pitch so that there is at least one macrofab process which can route it. Further work on draft placement. Everything is kinda on the boa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
    [joule_shield.brd, joule_shield.sch]
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2016-12-02 joule_shield: Connected up usb power switch enable and fault lines to GPIO pins. Switched to smaller mosfets instead of MF house bipolars.
    [joule_shield.brd, joule_shield.sch]
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2016-12-02 joule shield: Run ERC and connect up some wires which were inadvertently left unconnected.
    [joule_shield.brd, joule_shield.sch]
2016-12-02 joule shield: Resolve some DRC errors.
    [joule_shield.brd]
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2016-12-03 joule shield: Do grounds for things up through the SD level converter.
    [joule_shield.brd, joule_shield.sch]
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2016-12-04 joule shield: Get part numbers and populate attributes in for all parts.
    [joule_shield.brd, joule_shield.sch]
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2016-12-05 joule shield: Create script to "unroute" the auto-routed portion of the board.
    [joule_shield.brd]
2016-12-05 gimbal: Start work on updating gimbal board to support mounting a joule shield on top of it.
    [gimbal.brd, gimbal.sch]
2016-12-07 gimbal: Move parts around to roughly correct location and add in plane polygons.
    [gimbal.brd]
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2017-06-13 Provide a mechanism to write raw received frames to disk
    This can be helpful in analyzing the h264 bitstream or other protocol
    level failures.
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2018-07-30 Fix part number on regulator to HSOP-8 package
    [pi3_hat.brd, pi3_hat.sch]
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2018-08-13 Current errata for pi3 hat
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2019-02-28 gimbal: Replace 10uF cap with one that exists
    [gimbal.brd, gimbal.sch]
2019-03-09 pi3_hat: Relocate the PCB files to a subdirectory. Mark an errata
    [pi3_hat.brd, pi3_hat.sch]
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2019-04-28 Fix all the signs for the moteus config
    [moteus_ik.cfg]
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2019-04-30 Note an ERRATA w/ the r4 gimbal board
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2019-05-02 Fix the IK to be correct!
    [moteus_ik.cfg]
2019-05-02 Make sitting and standing more reliable
    This does the stand and sit part in IK space, but not yet the
    prepositioning.
    During prepositioning, instead we now gradually ramp up the power of
    the tibias so as to avoid them getting stuck on the ground. Talk
    about breaking abstraction layers Batman!
    [servo_interface.h]
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2019-05-03 When we see an error, cut power to everything
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2019-05-06 Support feed-forward torques
    This just compensates for the mass of the robot by assuming that much
    Z force is required at all times, distributed among all legs which are
    in contact with the ground. Assuming an appropriately set mass, this
    results in less sag during flight periods.
    [servo_interface.h]
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2019-05-08 Correct some signs on torque calcuations
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2019-05-14 Stop commanding a speed during the sit and stand phase
    We are now interpolating IK, and commanding a speed just resulted in a
    steady state position error, making the legs slide around.
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2019-09-20 moteus_servo: Implement a configurable global maximum torque
    This can be used to test things that might otherwise result in crazy
    movements, without too much risk of destroying the machine.
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2019-09-20 Implement a more relaxed startup sequence that works from the ground
    "resting" legs are no longer needed. After standing, the machine
    takes a step to get into the normal walking position. Before sitting,
    it takes a step to get into the squatting position.
    [moteus_ik.cfg]
2019-09-21 Fix signs of all femurs and tibias
    [moteus_ik.cfg]
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2019-10-04 When a servo fault occurs, command the kPositionTimeout mode
    This should reduce the amount of damage that occurs during a fall, as
    at least some of the servos will cushion the fall.
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2019-10-16 new-IK constify and fix frame name
2019-10-16 Beginnings of a new top level control scheme
    It runs on the rpi, but is likely broken in many ways
    [quada0.cfg]
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2019-10-18 Get standing up to work
    Also, robustify things against missing replies
    [quadruped_control.cc, quadruped_control.h]
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2019-10-21 Make the jump mode actually work
    * Fix an off by 10 unit error when calculating force from acceleration
    * When landing, start the z profile from the current position
    * When in flight, don't start landing if there is no force yet
    * When in flight, wait for some amount of time of valid criteria
    before switching to landing
    [quadruped_control.cc]
2019-10-21 Further improve jumps * A single jump now reverts to rest mode * You can command something other than jump and not read an unset optional
    [quadruped_control.cc]
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2019-10-29 Record missing replies in the binary log instead of text
    [quadruped_control.cc, quadruped_control.h]
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2020-02-27 Stub implementation of hat based AsioClient
    Compiles but doesn't work
    [rpi3_hat_spidev.cc]
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2020-02-27 Fix enough rpi3 hat things so that at least 2 devices per bus works
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2020-03-06 Make it possible to, and then invert the front legs
    Now we don't look quite so silly walking around by default, although
    when the feet placement are symmetric, the range of motion is reduced.
    [quada1.cfg]
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2020-03-19 Fix two minor problems with jumping
    1. We were erroneously using the landing acceleration for the pushing
    phase as well
    2. The final cycle of landing was using an inappropriate extra Z force
    [quadruped_control.cc]
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2020-03-25 Populate simulation with something of roughly correct dimensions
    [quadruped_config.h, quadruped_control.cc]
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2020-04-07 Improve the jumping heuristics
    Now, we reliably switch to landing mode shortly after touching the
    ground, since we just look for displacement instead of velocity.
    Also, continually calculate a trajectory when landing so we
    semi-accurately approach the bottom of the jump. This still doesn't
    work all that well yet, so impose a minimum downward velocity also.
    [quada1.cfg]
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2020-04-25 Remove an unused include and fix the fallout
    [quadruped_control.cc, quadruped_control.h]
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2020-04-27 Actually report the timestamp again
    This was broken by 50a5ad5443fe305bfe79968b803bc44f36e4da29
    [quadruped_control.cc]
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2020-04-28 Tweak constants so to land the flip at 0.85 max torque
    [quada1.cfg]
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2020-05-03 Fix off by one error that allows maximum-size CAN frames to be sent
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2020-05-09 tplot2: Fix seeking
    Turns out std::map::insert doesn't overwrite.
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2020-05-15 Make a "reset view" button
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2020-05-15 Render the ground and fix attitude transformation
    In the process, move the model transform back into C++ to make it
    easier to ensure the ground is rendered with a known transform in the
    "attitude enabled" case.
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2020-05-23 When jumping, don't go back to rest, since it prevents non-repeat operation
    [quadruped_control.cc]
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2020-05-27 Correctly calculate velocities while moving
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2020-06-06 Work towards making jump work in the new low-gain world
    It doesn't work great yet on the robot. I think we need feedforward
    accelerations to make tracking work better during retract.
    [quadruped_config.h, quadruped_control.cc]
2020-06-06 Explicitly command acceleration of each leg
    This removes some "extra_z" hacks, and makes it possible for the lower
    level controller to apply a feed forward term based on the joint
    acceleration. This doesn't end up working all that well, as the
    unloaded leg isn't that well approximated by a point mass, but it is
    more sound and reduces the number of special cases.
    Re-work the standup logic to use this framework, as well as give it
    acceleration limited tweens into the final position.
    [quada1.cfg]
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2020-06-12 Initial conversion to use the new pi3hat firmware and software library
    This still has some performance issues
    [quadruped_control.cc, quadruped_control.h, turret_control.cc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]
2020-06-13 Many timing fixes for new pi3hat library
    [quadruped_control.cc, quadruped_control.h]
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2020-06-18 Report when we skip a cycle
    [quadruped_control.cc]
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2020-06-24 Use the correctly named "M" frame
2020-06-24 Directly log the MB frame and use that to simplify frame registration in tplot
    The MB frame currrently isn't configured with the correct offset (as
    that was the previous tplot2 behavior as well).
    [quadruped_control.cc]
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2020-06-26 Be smarter about picking swing legs after reversing
    Previously, we would just always pick the same foot. Now we look to
    see which one would result in moving over a balance point. (We'd do
    this every time, except we don't yet have a check on time to
    infeasibility).
2020-06-26 Optionally start the simulated yaw from a cmdline offset
    In real life the initial reported yaw is arbitrary. This can help
    discover problems where we depend on it being a certain way.
2020-06-26 Adjust CoM location based on an estimate of the current terrain
    This changes a number of things:
    First, the RB offset is no longer commandable across all gaits. There
    is instead a "rest" only option to add an additional offset to that
    command.
    Second, there is a new "T" frame, which is an estimate of the terrain
    under the robots feet. That is estimated recursively based on feet
    that are marked as being in stance and the current M frame with an
    exponential filter.
    Finally, all the gaits now apply a RB offset to get the CoM to be over
    the center of support based on the current terrain. This lets it walk
    over the simulated ramp of size up to 0.35, (and 0.4 backwards).
    [quada1.cfg]
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2020-07-09 Fault if the voltage gets too low
    [quadruped_config.h, quadruped_control.cc]
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2020-08-01 Fix sign conventions so that CoM renders correct in tplot2
    This changes the strategy for selecting the RB transform to one that
    is hopefully as sound, but also works when everything has the correct
    sign.
    [quadruped_control.cc]
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2020-08-04 Provide buttons to reset to known camera locations
    Also provide a non-functional switch between perspective and ortho modes
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2020-08-05 First pass at an improved trot gait
    There are still some outstanding usability issues, like making it
    easier to drive in low speed, and also the stability at high speed
    still isn't great.
    [quada1.cfg]
2020-08-07 Fix conflation of M frame
    We were in some places assuming the M frame was locked to the gyro
    heading, and other places assuming it was locked to the body heading.
    Make two separate frames with those two conventions and use them where
    appropriate.
    The net result was that the CoM was accounted for incorrectly, in a
    way that would vary depending upon which direction the robot was
    pointed!
    While we are at it, make tplot2 able to view from any of the relevant
    frames, and make it able to show commanded support regions, to make
    debugging these types of problems easier.
    [quadruped_control.cc]
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2020-09-02 Build the simulator dynamically linked
    Statically linked binaries can cause problems with mesa drivers that
    also link to libstdc++.
2020-09-04 Calculate joint velocities using the current, not ideal positions
    We were already doing this for torque, and it makes sense to do it for
    velocities too. Near extremal positions, the velocities can change
    drastically, which can result in force application in significantly
    the wrong direction.
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2020-09-04 Add a double check to prevent negative servo gains
    [quadruped_control.cc]
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2020-09-04 Make the trot gait more robust
    This includes several changes to smooth out transitions in the trot
    gait, making it stable across a wider range of speeds and terrains:
    * When nearing the end of the flight phase, scale the kp and kd of
    the leg, gradually ramping them back up after the foot is in
    stance.
    * When first in stance, start with a stance value < 1.0 and gradually
    ramp it up. When other legs are already down, this makes the
    transition of force more gradual (but doesn't change anything if
    we're landing from a flight phase).
    * Use a heuristic to detect when a leg first makes contact with the
    ground. When it does, reset the control position to the actual
    positio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
    [quada1.cfg]
2020-09-09 Simplify the restorative velocity calculation by saving some state and no longer ramping it down
    [quadruped_config.h]
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

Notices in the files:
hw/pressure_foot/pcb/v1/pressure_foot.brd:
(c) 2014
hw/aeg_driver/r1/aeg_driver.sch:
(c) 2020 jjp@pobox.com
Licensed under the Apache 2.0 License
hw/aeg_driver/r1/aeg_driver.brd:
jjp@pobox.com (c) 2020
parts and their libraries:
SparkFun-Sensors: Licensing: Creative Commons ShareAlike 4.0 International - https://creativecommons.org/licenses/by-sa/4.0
